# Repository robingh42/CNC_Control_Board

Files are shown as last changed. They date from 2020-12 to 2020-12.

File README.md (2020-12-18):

A general purpose CNC PCB utilizing the Teensy 3.6 micro controller

Check out the [project description](https://robingh.com/portfolio/CNC_Board.html)

To use this repo:

1. Clone this repo to your machine
2. Add the [Digikey KiCad Library](https://www.digikey.com/en/resources/design-tools/kicad) to KiCad

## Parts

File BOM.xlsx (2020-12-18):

Ref | Component | Adafruit | Other | DK | Quantity | Cost | Sum
 | Steppers
> A1-A3 | Pololu_Breakout_DRV8825 | https://www.pololu.com/product/2982 | https://www.amazon.com/KINGPRINT-DRV8825-Stepper-Driver-Printer/dp/B075XH1TSJ | 2183-2977-ND | 3 | 2.398 | 7.19
 | CONN HDR 8POS 0.1 TIN PCB |  |  | ‎S7006-ND‎ (https://www.digikey.com/product-detail/en/PPTC081LFBN-RC/S7006-ND/810147/?itemSeq=347653444) | 6 | 0.608 | 3.65
> C1-C3 | 100 uF Capacitor |  |  | UPS1H101MPD-ND‎ | 3 | 0.338 | 1.01
> J9, J11, J13 | Molex Stepper Conn |  |  | WM4202-ND‎ | 3 | 0.27 | 0.81
> J8, J10, J12 | Micro_Stepping |  |  | 609-2583-ND‎ | 3 | 0.75 | 2.25
 | MINITEK JUMPER |  |  | ‎609-5221-ND‎ (https://www.digikey.com/product-detail/en/86730-301LF/609-5221-ND/5967789/?itemSeq=347653434) | 9 | 0.38 | 3.42
 | Teensy
U1 | Teensy3.6 | 3266 | https://www.pjrc.com/store/teensy36_pins.html | 1568-1442-ND | 1 | 33.25 | 33.25
 | CONN HDR 24POS 0.1 TIN PCB |  |  | ‎S7022-ND‎ (https://www.digikey.com/product-detail/en/PPTC241LFBN-RC/S7022-ND/810162/?itemSeq=347653443) | 2 | 1.37 | 2.74
 | Capacitors
C6 | 10 uF Capacitor |  |  | 493-11317-1-ND | 1 | 0.24 | 0.24
> C5, C8 | 100 uF Capacitor |  |  | 493-5356-1-ND | 2 | 0.221 | 0.44
> C4, C7, C9 | 0.1 uF Capacitor |  |  | 399-9824-ND | 3 | 0.22 | 0.66
 | LEDs
D1 | LED 3mm |  |  | ‎160-1959-ND‎ | 1 | 0.39 | 0.39
D2 | LED 3mm |  |  | 160-1957-ND‎ | 1 | 0.39 | 0.39
> R1, R2 | 100 Ohm 1/4W Resistor |  | https://www.amazon.com/gp/product/B01HRR7EBG/ref=ppx_yo_dt_b_asin_title_o03_s00?ie=UTF8&psc=1 | 100XBK-ND | 2 | 0.1 | 0.20
 | 12V Output (solenoid)
D3 | 1N4004 Diode |  |  | ‎1N4004-E3/54GICT-ND‎ | 1 | 0.21 | 0.21
J15 | Solenoid connector |  | https://www.amazon.com/Tulead-Solenoid-Electronic-Actuator-Electromagnet/dp/B07VC5JKYG | 102-6171-ND | 1 | 0.78 | 0.78
R3 | 10K Ohm 1/4W Resistor |  |  | 10.0KXBK-ND | 1 | 0.1 | 0.10
 | MOSFET |  |  | IRLB8721PBF-ND | 1 | 0.93 | 0.93
 | Connectors
J1 | Analog_Conn |  |  | ‎S7006-ND‎ (https://www.digikey.com/product-detail/en/PPTC081LFBN-RC/S7006-ND/810147/?itemSeq=347653444) | 1 | 0.608 | 0.61
J2 | Digital_Conn |  |  | ‎S7006-ND‎ (https://www.digikey.com/product-detail/en/PPTC081LFBN-RC/S7006-ND/810147/?itemSeq=347653444) | 1 | 0.608 | 0.61
> J4-J6 | Limit_Switch_Conn | 819 |  | WM2700-ND | 3 | 0.4 | 1.20
J14 | Servo_Conn |  |  | WM4201-ND | 1 | 0.24 | 0.24
 | Power
J7 | Barrel_Jack |  |  | ‎PJ-002AH | 1 | 0.74 | 0.74
S1 | SWITCH TOGGLE SPDT 5A 120V |  |  | EG2362-ND | 1 | 2.67 | 2.67
U2 | 5V_Buck_Conv |  |  | 2183-2850-ND | 1 | 10.95 | 10.95
 | User Interface
J3 | I2C_Conn |  |  | S7002-ND | 1 | 0.45 | 0.45
SW1 | Rotary_Encoder_Switch | 377 |  |  | 1 | 1.57 | 1.57
U3 | I2C_OLED_.96" |  | https://www.amazon.com/DIYmall-Serial-128x64-Display-Arduino/dp/B00O2KDQBE?th=1 |  | 1 | 8.99 | 8.99
 |  |  |  |  |  | Total: | 86.69
 | Already owned
 | CONN 22-30AWG CRIMP TIN |  |  | ‎WM2756-ND‎ (https://www.digikey.com/product-detail/en/0008650805/WM2756-ND/1130600/?itemSeq=347653436) | 20 | 0.17 | 3.40
 | CONN HOUS 4POS .100 W/RAMP/RIB |  |  | WM2002-ND | 3 | 0.21 | 0.63
 |  |  |  | ‎WM2011-ND‎ (https://www.digikey.com/product-detail/en/0022012027/WM2011-ND/171991/?itemSeq=347653498) | 3 | 0.11 | 0.33
M4 | Stepper_Motor |  |  |  | 3 | 0 | 0.00
Q1 | Motor_Servo |  |  |  | 1 | 0 | 0.00
 |  |  |  |  |  | Total: | 4.36

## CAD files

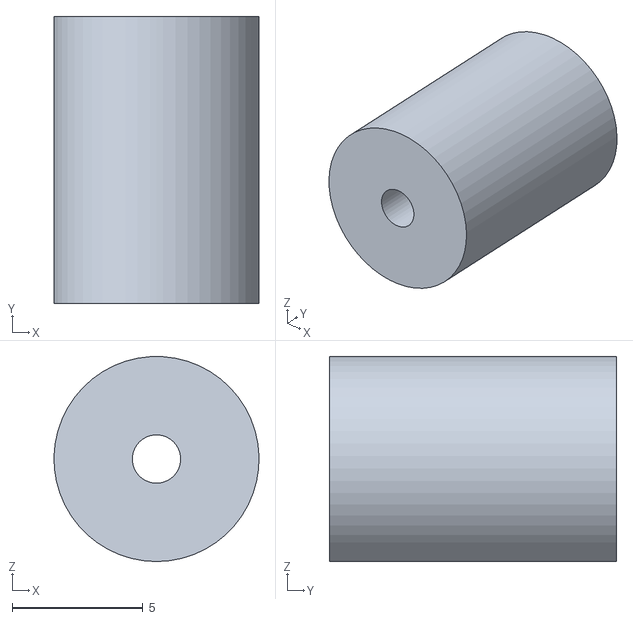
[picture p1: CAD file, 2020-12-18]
CAD/Standoff.STL
7.85 x 11.0 x 7.85

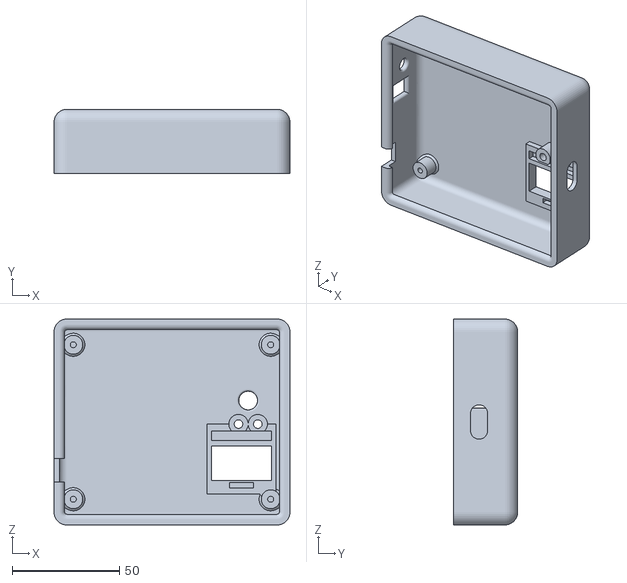
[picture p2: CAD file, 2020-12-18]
CAD/BoxTop_final.STL
110.0 x 30.0 x 96.0

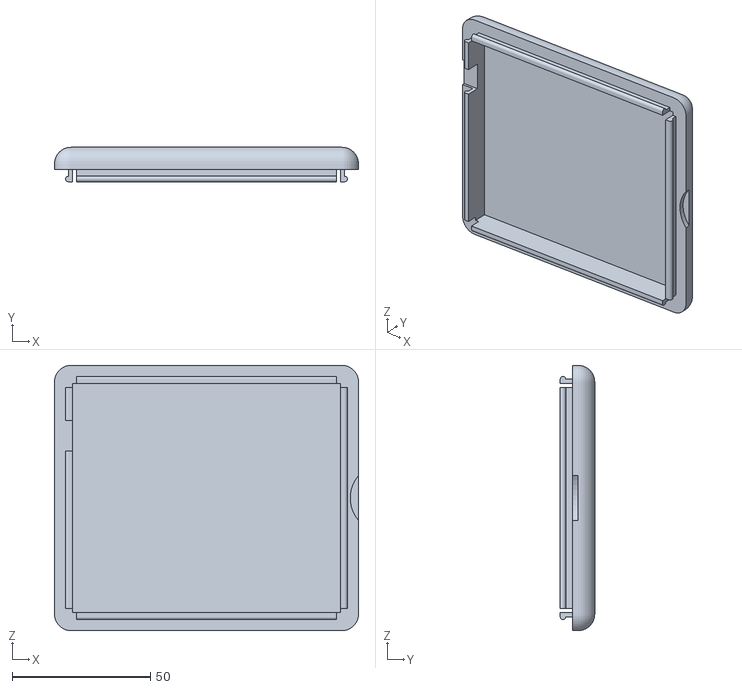
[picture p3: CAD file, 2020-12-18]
CAD/BoxBottom_final.STL
110.0 x 12.5 x 96.0

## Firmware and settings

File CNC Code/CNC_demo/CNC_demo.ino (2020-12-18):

/* Written by Robin Graham-Hayes
 * 
 * A example of what the CNC board can do
 *  
 * I own no rights to the libraries
 *  
 *  
*/
#include <Wire.h>
#include <Adafruit_GFX.h>
#include <Adafruit_SSD1306.h>
#define ENCODER_USE_INTERRUPTS
#include <Encoder.h>
#include <Arduino.h>
#include "BasicStepperDriver.h"
#include <Servo.h>


#define SCREEN_WIDTH 128 // OLED display width, in pixels
#define SCREEN_HEIGHT 64 // OLED display height, in pixels
#define OLED_RESET 4
Adafruit_SSD1306 display(SCREEN_WIDTH, SCREEN_HEIGHT, &Wire, OLED_RESET);


Encoder myEnc(11, 12);
volatile long oldPosition  = -999;
volatile long newPosition = 0;
volatile int pos = 0;
int encoderSteps = 4;
int menu_len = 5;

const int button_pin = 10;
volatile int button_state = 0; //starting state of the button is 0
volatile bool in_menu = true;
unsigned long last_interrupt_time = 0; 

int solenoid_pin = 9;

const int LED_GREEN = 14;
const int LED_RED = 13;


int servo_pin = 8;
Servo myservo;

#define MOTOR_STEPS 400
#define Z_MOTOR_STEPS 200
#define RPM 120
// Since microstepping is set externally, make sure this matches the selected mode
// If it doesn't, the motor will move at a different RPM than chosen
// 1=full step, 2=half step etc.
#define MICROSTEPS 32
#define x_DIR 23
#define x_STEP 22
#define y_DIR 7
#define y_STEP 6
#define z_DIR 6
#define z_STEP 5

// 2-wire basic config, microstepping is hardwired on the driver
BasicStepperDriver stepperX(MOTOR_STEPS, x_DIR, x_STEP);
BasicStepperDriver stepperY(MOTOR_STEPS, y_DIR, y_STEP);
BasicStepperDriver stepperZ(Z_MOTOR_STEPS, z_DIR, z_STEP);



const unsigned char bitmap[] = {
  0x3f, 0xff, 0xff, 0xe0, 0x00, 0x00, 0x00, 0x00, 0x7f, 0xff, 0xff, 0xf8, 0xe0, 0x00, 0x03, 0x80,
  0x7f, 0xff, 0xff, 0xf8, 0xe0, 0x00, 0x03, 0x80, 0x7f, 0xff, 0xff, 0xf0, 0xe0, 0x00, 0x03, 0x80,
  0x70, 0x00, 0x00, 0x00, 0xe0, 0x00, 0x03, 0x80, 0x70, 0x00, 0x00, 0x00, 0xe0, 0x00, 0x03, 0x80,
  0x70, 0x00, 0x00, 0x00, 0xe0, 0x00, 0x03, 0x80, 0x70, 0x00, 0x00, 0x00, 0xe0, 0x00, 0x03, 0x80,
  0x70, 0x00, 0x00, 0x00, 0xe0, 0x00, 0x03, 0x80, 0x70, 0x0f, 0xfc, 0x00, 0xe0, 0x00, 0x03, 0x80,
  0x70, 0x1f, 0xfe, 0x00, 0xe0, 0x00, 0x03, 0x80, 0x70, 0x1f, 0xff, 0x00, 0xe0, 0x00, 0x03, 0x80,
  0x70, 0x1f, 0xff, 0x00, 0xe0, 0x00, 0x03, 0x80, 0x70, 0x1c, 0x0f, 0x00, 0xe0, 0x00, 0x03, 0x80,
  0x70, 0x1c, 0x0f, 0x00, 0xe0, 0x00, 0x03, 0x80, 0x70, 0x1c, 0x0f, 0x00, 0xe0, 0x00, 0x03, 0x80,
  0x70, 0x1e, 0x0f, 0x00, 0xe0, 0x00, 0x03, 0x80, 0x70, 0x1f, 0xff, 0x00, 0xe0, 0x00, 0x03, 0x80,
  0x70, 0x1f, 0xfe, 0x00, 0xe0, 0x00, 0x03, 0x80, 0x70, 0x1f, 0xfc, 0x00, 0xe0, 0x00, 0x03, 0x80,
  0x70, 0x1c, 0x38, 0x00, 0xe0, 0x00, 0x03, 0x80, 0x70, 0x1c, 0x3c, 0x00, 0xe0, 0x00, 0x03, 0x80,
  0x70, 0x1c, 0x1c, 0x00, 0xe0, 0x00, 0x03, 0x80, 0x70, 0x1c, 0x1e, 0x00, 0xe0, 0x00, 0x03, 0x80,
  0x70, 0x1c, 0x1e, 0x00, 0xe0, 0x00, 0x03, 0x80, 0x70, 0x1c, 0x0e, 0x00, 0xff, 0xff, 0xff, 0x80,
  0x70, 0x1c, 0x0e, 0x00, 0xff, 0xff, 0xff, 0x80, 0x70, 0x08, 0x06, 0x00, 0xff, 0xff, 0xff, 0x80,
  0x70, 0x00, 0x00, 0x00, 0xff, 0xff, 0xff, 0x80, 0x70, 0x00, 0x00, 0x00, 0xe0, 0x00, 0x03, 0x80,
  0x70, 0x00, 0x00, 0x00, 0xe0, 0x00, 0x03, 0x80, 0x70, 0x00, 0x00, 0x00, 0xe0, 0x00, 0x03, 0x80,
  0x70, 0x00, 0x00, 0x00, 0xe0, 0x00, 0x03, 0x80, 0x70, 0x00, 0xff, 0xf0, 0xe0, 0x00, 0x03, 0x80,
  0x70, 0x01, 0xff, 0xf8, 0xe0, 0x00, 0x03, 0x80, 0x70, 0x00, 0xff, 0xf8, 0xe0, 0x00, 0x03, 0x80,
  0x70, 0x00, 0x7f, 0xf8, 0xe0, 0x00, 0x03, 0x80, 0x70, 0x00, 0x00, 0x38, 0xe0, 0x00, 0x03, 0x80,
  0x70, 0x00, 0x00, 0x38, 0xe0, 0x00, 0x03, 0x80, 0x70, 0x00, 0x00, 0x38, 0xe0, 0x00, 0x03, 0x80,
  0x70, 0x00, 0x00, 0x38, 0xe0, 0x00, 0x03, 0x80, 0x70, 0x00, 0x00, 0x38, 0xe0, 0x00, 0x03, 0x80,
  0x70, 0x00, 0x00, 0x38, 0xe0, 0x00, 0x03, 0x80, 0x70, 0x00, 0x00, 0x38, 0xe0, 0x00, 0x03, 0x80,
  0x70, 0x00, 0x00, 0x38, 0xe0, 0x00, 0x03, 0x80, 0x70, 0x00, 0x00, 0x38, 0xe0, 0x00, 0x03, 0x80,
  0x70, 0x00, 0x00, 0x38, 0xe0, 0x00, 0x03, 0x80, 0x70, 0x00, 0x00, 0x38, 0xe0, 0x00, 0x03, 0x80,
  0x70, 0x00, 0x00, 0x38, 0xe0, 0x00, 0x03, 0x80, 0x70, 0x00, 0x00, 0x38, 0xe0, 0x00, 0x03, 0x80,
  0x7f, 0xff, 0xff, 0xf8, 0xe0, 0x00, 0x03, 0x80, 0x7f, 0xff, 0xff, 0xf8, 0xe0, 0x00, 0x03, 0x80,
  0x7f, 0xff, 0xff, 0xf8, 0xe0, 0x00, 0x03, 0x80, 0x3f, 0xff, 0xff, 0xf0, 0x40, 0x00, 0x00, 0x00
};


void setup() {
  Serial.begin(9600);
  //Setup I2C pins for display
  Wire.setSDA(17);
  Wire.setSCL(16);

  //Setup the servo
  myservo.attach(servo_pin);

  pinMode(LED_GREEN, OUTPUT);
  pinMode(LED_RED, OUTPUT);
  digitalWrite(LED_RED, HIGH);
  
  //Setup the encoder button
  pinMode(button_pin, INPUT_PULLUP);
  
  //interrupt if the state of the button changes
  attachInterrupt(digitalPinToInterrupt(button_pin), buttonISR, CHANGE);
  
  //Setup the solenoid
  pinMode(solenoid_pin, OUTPUT);
  
  //Setup the steppers with the programed microsteps
  stepperX.begin(RPM, MICROSTEPS);
  stepperY.begin(RPM, MICROSTEPS);

  // If the display throws an error, do not continue
  // SSD1306_SWITCHCAPVCC = generate display voltage from 3.3V internally
  if (!display.begin(SSD1306_SWITCHCAPVCC, 0x3C)) { // Address 0x3D for 128x64
    Serial.println(F("SSD1306 allocation failed"));
    for (;;); // Don't proceed, loop forever
  }

  
  display.clearDisplay();
  int start_width = 58;
  int start_height = 54;
  display.drawBitmap(64 - start_width / 2, 32 - start_height / 2, bitmap, start_width, start_height, SSD1306_WHITE);
  display.display();
  delay(2000); // Pause for 2 seconds

  // Clear the buffer
  display.clearDisplay();
  display.setTextSize(1);      // Normal 1:1 pixel scale
  display.setTextColor(SSD1306_WHITE); // Draw white text
  display.setCursor(1, 0);     // Start at top-left corner
  display.cp437(true);         // Use full 256 char 'Code Page 437' font
  updateMenu(0);

}

void loop() {
  menu();
  
  //Serial.print("menu ");
  //Serial.println(in_menu);
  //  display.invertDisplay(true);
  //  delay(1000);
  //  display.invertDisplay(false);
  //  delay(1000);
}




/*#################################################################
  #                           View                                #
  #################################################################*/
void updateMenu(long pos) {
  
  Serial.println("update menu");
  display.clearDisplay();
  display.setTextSize(1);      // Normal 1:1 pixel scale
  display.setCursor(2, 2);
  display.println("Sweep Stepper");
  display.setCursor(2, 10);
  display.println("Stepper Speed Test");
  display.setCursor(2, 18);
  display.println("Multi Axis Stepper");
  display.setCursor(2, 26);
  display.println("Sweep Servo");
  display.setCursor(2, 34);
  display.println("Blink Solenoid");
  display.setCursor(2, 42);
  display.println("Stepper from Encoder");
  display.setCursor(0, 50);
  display.fillRect(-1, pos * 8 + 1, 128, 9, SSD1306_INVERSE);
  display.display();
}

void show_func(String func_name, String action = "Running",  String func_name2 = ""){
  display.clearDisplay();
  display.setTextSize(2); 
  display.setCursor(SCREEN_WIDTH/2 - 10*(action.length()/2+1), SCREEN_HEIGHT/4 - 10);
  display.println(action);
  if (func_name2 == ""){
    display.setCursor(SCREEN_WIDTH/2 - 10*(func_name.length()/2+1), SCREEN_HEIGHT*3/4 - 14/2);
    display.println(func_name);
    display.display();
  }
  else {
    display.setCursor(SCREEN_WIDTH/2 - 10*(func_name.length()/2+1), SCREEN_HEIGHT*5/8 - 10);
    display.println(func_name);
    display.setCursor(SCREEN_WIDTH/2 - 10*(func_name2.length()/2+1), SCREEN_HEIGHT*7/8 - 14/2);
    display.println(func_name2);
    display.display();
  }
  
}

/*#################################################################
  #                       Controller                              #
  #################################################################*/

void menu() {
  digitalWrite(LED_GREEN, LOW);
  newPosition = -myEnc.read();
  pos = newPosition / encoderSteps;
  //  Serial.print("[");
  //  Serial.print(myEnc.read());
  //  Serial.print(pos);
  //  Serial.println("]");

  if (pos > menu_len) {
    myEnc.write(0);
    newPosition = 0;
    Serial.println(pos);
    Serial.println("upper");

  }
  else if (pos <= -1) {
    myEnc.write(0);
    newPosition = 0;
    Serial.print(pos);
  }

  if (newPosition != oldPosition) {
    oldPosition = newPosition;
    pos = newPosition / encoderSteps;
    updateMenu(pos);
    Serial.println(pos);
    Serial.println("change");
  }
  
  menu_selection();
}


void buttonISR() {
          //Serial.println("ISR");
  if (millis() - last_interrupt_time < 50) { //if the last interrupt happened within the last 50 milliseconds, do not change the mode
    return;
  }
          //Serial.println("buttonISR");
  last_interrupt_time = millis(); //set the new last interrupt time to the current millis value
  if (button_state == 1) { //if the button state is high, add one to the mode
    button_state = 0; //set the button state back to zero
    in_menu = !in_menu;
           //Serial.println("button");
  } else {
    button_state = 1; //set the button state to one so that we only recognize every other change
  }
}


void menu_selection() {
  if (in_menu){
    return;
  }
  digitalWrite(LED_GREEN, HIGH);
  switch (pos) {
    case (0)://all lights off
      Serial.print("sweep");
      stepper_sweep();
      break;
    case (1)://all lights off
      Serial.print("speed");
      stepper_speed();
      break;
    case (2)://all lights off
      Serial.print("multi");
      stepper_multi();
      break;
     case(3):
      Serial.print("Servo");
      servo_test();
      break;
     case(4):
      Serial.print("solenoid");
      solenoid_blink();
      break;
     case(5):
      Serial.print("stepFromEncoder");
      stepFromEncode();
      break;
  }
  Serial.println("--------");
  Serial.println(pos);
  Serial.println("--------");
  updateMenu(pos);
  
  if (!in_menu){
    in_menu = !in_menu;
  }
}


/*#################################################################
  #                          Model                                #
  #################################################################*/


void stepper_sweep() {
  show_func("Stepper","Sweeping");
  Serial.println("forward");
  stepperX.rotate(360);
  delay(500);
  Serial.println("back");
  stepperX.move(-MOTOR_STEPS*MICROSTEPS);
  delay(1000);
  Serial.println("stop");
}

void stepper_speed() {
  show_func(String("RPM:"+String(RPM)),"Stepper");
  int timeS = 500;
  stepperX.move(MOTOR_STEPS*MICROSTEPS);
  delay(timeS);
  stepperX.setRPM(RPM * 2);
  show_func(String("RPM:"+String(RPM * 2)),"Stepper");
  stepperX.move(MOTOR_STEPS*MICROSTEPS);
  delay(timeS);
  stepperX.setRPM(RPM * .5);
  show_func(String("RPM:"+String(int(RPM * .5))),"Stepper");
  stepperX.move(MOTOR_STEPS*MICROSTEPS);
  delay(timeS);
}

void stepper_multi() {
  show_func("Steppers","Running","X&Y");
  stepperX.rotate(360);
  delay(500);
  stepperX.move(-MOTOR_STEPS*MICROSTEPS);
  delay(1000);
  stepperY.rotate(360);
  delay(500);
  stepperY.move(-MOTOR_STEPS*MICROSTEPS);
  delay(1000);
}

void solenoid_blink() {
  show_func("Solenoid");
  for(int i = 0; i < 5; i++){
    digitalWrite(solenoid_pin, HIGH);
    delay(100);
    digitalWrite(solenoid_pin, LOW);
    delay(100);
  }
  
}

void servo_test(){
  show_func("Servo","Sweeping");
  for(int ang = 0; ang <= 180; ang += 1) // goes from 0 degrees to 180 degrees 
  {                                  // in steps of 1 degree 
    if (in_menu) {return;}
    myservo.write(ang);              // tell servo to go to position in variable 'pos' 
    //delay(15);                       // waits 15ms for the servo to reach the position 
  } 
  for(int ang = 180; ang>=0; ang-=1)     // goes from 180 degrees to 0 degrees 
  {                                
    if (in_menu) {return;}
    myservo.write(ang);              // tell servo to go to position in variable 'pos' 
    //delay(15);                       // waits 15ms for the servo to reach the position 
  } 

  for(int ang = 0; ang <= 180; ang += 15) // goes from 0 degrees to 180 degrees 
  {                                  // in steps of 1 degree 
    if (in_menu) {return;}
    myservo.write(ang);              // tell servo to go to position in variable 'pos' 
    delay(500);                       // waits 15ms for the servo to reach the position 
  } 
  for(int ang = 180; ang>=0; ang-= 15)     // goes from 180 degrees to 0 degrees 
  { 
    if (in_menu) {return;}                        
    myservo.write(ang);              // tell servo to go to position in variable 'pos' 
    delay(500);                       // waits 15ms for the servo to reach the position 
  } 
  
}
void stepFromEncode(){
  int tot = 0;
  //myEnc.write(0);
  while (!in_menu){
    int rot = encoderMotor();
    tot += rot*15;
    tot = tot % 360;
    stepperX.rotate(15*rot);
    display.clearDisplay();
    display.setTextSize(1); 
    display.setCursor(SCREEN_WIDTH/2 - 5*9,2);
    display.println("Stepper Position:");
    display.setTextSize(3);      // Normal 1:1 pixel scale
    if (abs(tot) > 99){
      display.setCursor(SCREEN_WIDTH/2 - 30, SCREEN_HEIGHT/2 - 21/2);
    }
    else {
      display.setCursor(SCREEN_WIDTH/2 - 15, SCREEN_HEIGHT/2 - 21/2);
    }
    display.println(tot);
    display.display();
  }
}


int encoderMotor(){
  newPosition = -myEnc.read();
  //Serial.print("New pos: ");
  //Serial.println(newPosition);
  pos = newPosition / encoderSteps;

  if (newPosition != oldPosition) {
    
    int oldPos = oldPosition / encoderSteps;
    int change = pos - oldPos;
    oldPosition = newPosition;
    pos = newPosition / encoderSteps;
    Serial.println(pos);
    Serial.println(newPosition);
    Serial.println(oldPos);
    Serial.print(change);
    Serial.println(" change");
    return change;
  }
    return 0;


}
